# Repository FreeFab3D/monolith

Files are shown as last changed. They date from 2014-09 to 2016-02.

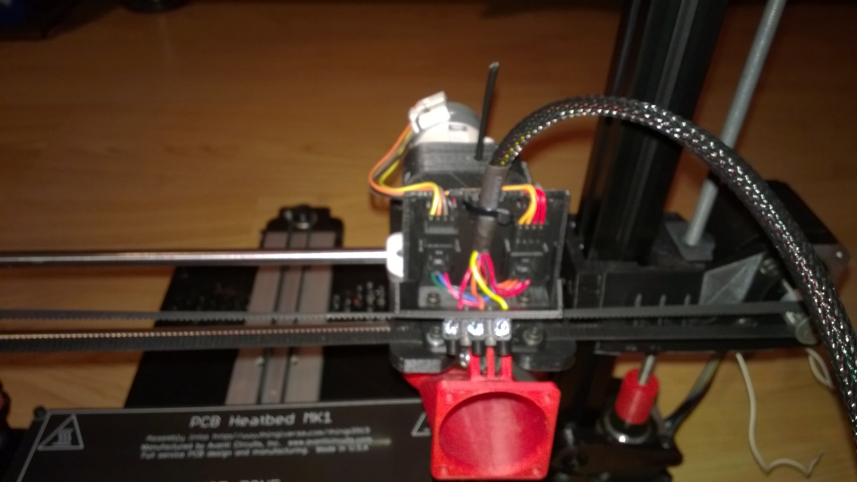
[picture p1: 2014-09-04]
build photos/WP_20140312_003.jpg

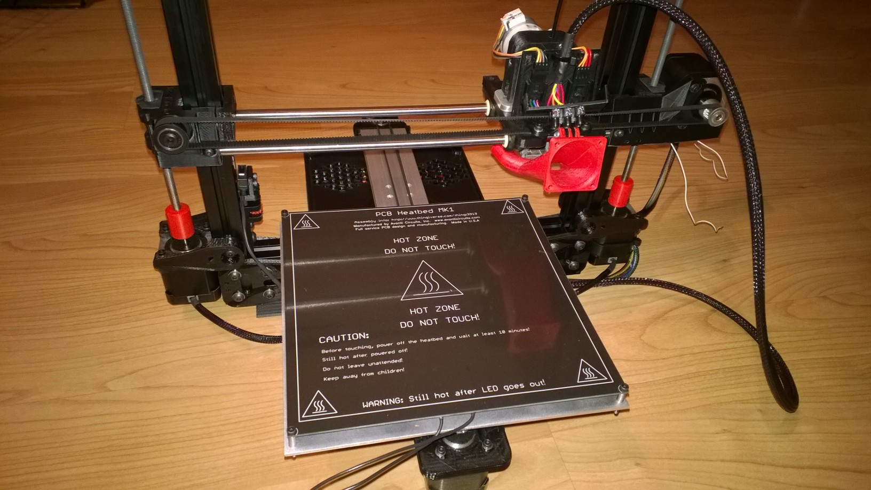
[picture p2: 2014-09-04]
build photos/WP_20140312_004.jpg

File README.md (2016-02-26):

# FreeFab 3D Monolith 3D Printer

## Features
- Hybrid design combining the best of the Bukobot and MendelMax
- 200mm x 200mm x 200mm (8" x 8" x 8") build area
- 120mm/minute speed
- 0.1 - 0.25mm layer height
- 3mm filament-based feed stock
- Heated bed to print ABS, PLA and other plastics
- Hexagon hot-end and RAMBo control board
- Flexible and advanced open-source design, including a USB interface
- LED extrusion lamps
- Compact precision aluminum frame

## Repo Layout

### Build Photos
Various photos showing close-ups of the machine to help while building. 

### Firmware
Marlin firmware for the RAMBo Arduino control boards. One version is for the Monoliths using an LCD displau board.

### Settings
Screen shots showing settings for Repetier-Host and Slic3r config ini profiles. 

### STLs
All the plastic parts required to build the Monolith. In some cases more than one version of the same part are included, ie: Y-foot and Z-rod caps. You can choose which version you like best. 

All parts should be printed using good quality ABS except the control board box and lid, which should be printed in PLA. Micro extruder needs at least 30% infill (40% is better), but other parts should use between 20% and 30% infill. 

This work is licensed under a Creative Commons Attribution 4.0 International License.

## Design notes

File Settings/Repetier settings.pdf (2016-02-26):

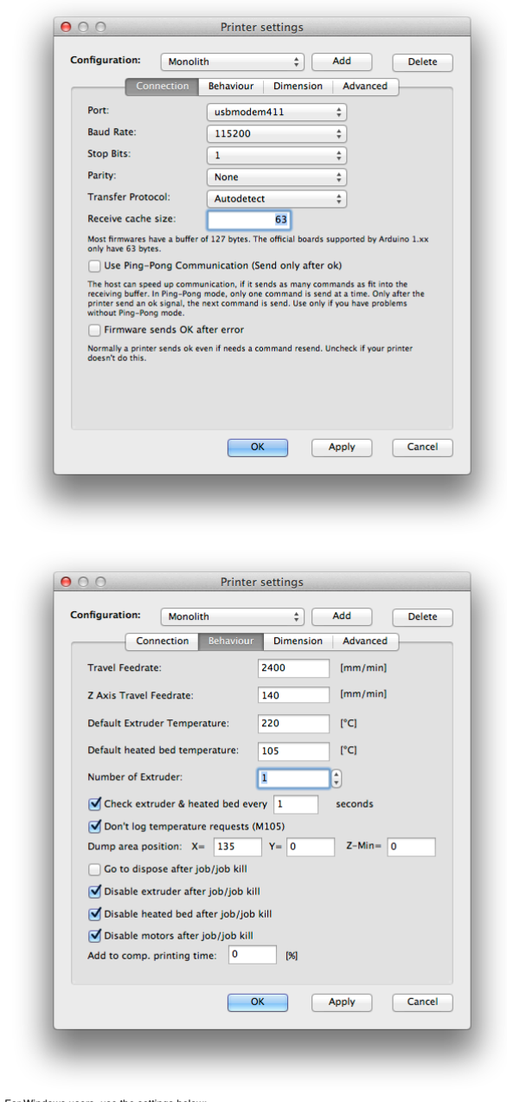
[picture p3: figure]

For Windows users, use the settings below:

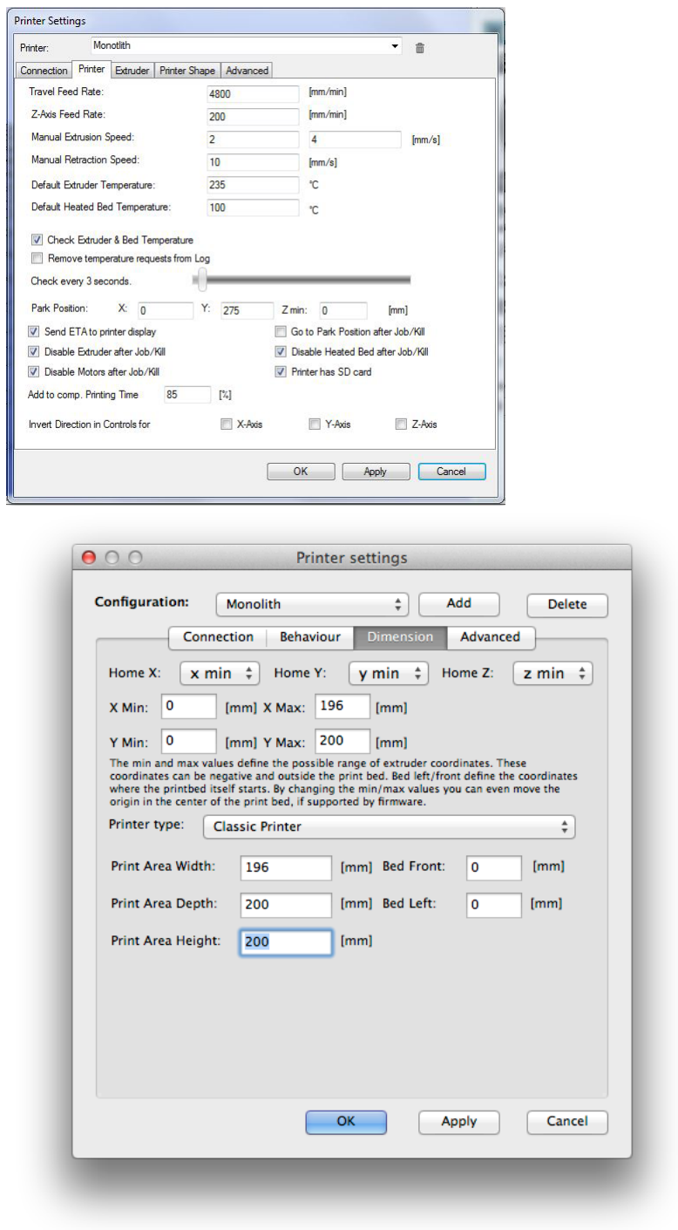
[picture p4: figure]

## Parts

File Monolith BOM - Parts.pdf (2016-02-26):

ML1 Parts | Qty. | Description | Mfg. Part # | Unit cost | Ext. Cost | Supplier | Comments
Frame | 2 | Aluminum Frame - side rails | HFSB5-2525-460 | $7.68 | $15.36 | us.misumi-ec.com | no price break <20+
| 1 | Aluminum Frame - top rail | HFSB5-2525-285 | $4.72 | $4.72 | us.misumi-ec.com | Price break @10
| 1 | Aluminum Frame - bottom rail | HFSB5-2550-285 | $8.04 | $8.04 | us.misumi-ec.com | Price break @10
| 1 | Aluminum Frame - y axis | HFSQN4-1050-345 | $5.96 | $5.96 | us.misumi-ec.com | no price break <75
| 2 | Smooth Rods | PSFG8-375 | $7.17 | $14.34 | us.misumi-ec.com | Price break @4 - Old rods were RGOC8-375
Printbed | 1 | Y carriage Plate | 8.625 with hole pattern | $11.15 | $11.15 | Laserfab.net | Price includes shipping.
| 1 | Y Glass | 8.375 x 7.9375 x .125" | $4.00 | $4.00 | St Pete Glass & Mirror, 5565 64th Way N, St Pete
| 1 | PCB Black | custom order | $26.00 | $26.00 | AvantiCircuits.com | Price includes shipping.
Pulleys | 2 | Pulley - 20 tooth aluminum | 210 | $5.50 | $11.00 | OpenBuilds.com | Possible alt = B&B Manufacturing
Belts | 4' | 6mm GT2 Belt | GT2 Timing Belt | $2.66 | $10.64 | Ultibots.com | Price break @20m
X Idler | 1 | Vslot Idler | 550-PACK | $4.85 | $4.85 | OpenBuilds.com | Price break @20
Wheels | 4 | Vslot Wheel Kits - Delrin | 500-Pack | $4.13 | $16.50 | OpenBuilds.com | Price break @20 - Includes Shipping
| 4 | Spacer, #10 hole, 1/4" tall, AL | 6TA23 | $0.42 | $1.69 | Grainger | Price includes shipping
Bearings | 5 | 8mm x 22mm 608-ZZ Bearing | 0474510 | $0.79 | $3.94 | Fastenal
| 4 | Pillow block bearing | KSTM-08 | $2.54 | $10.16 | Igus.com
Extruder motor | 1 | PG35L geared stepper motor | PG35L | $23.70 | $23.70 | Ultibots.com | Price break @5
Heat sink | 1 | PG35L short fin heat sink | PG35L short fin heat sink | $7.95 | $7.95 | Ultibots.com
Extruder hardware | 1 | Micro-extruder kit | MEV5HWK3 | $22.95 | $22.95 | Ultibots.com | Price break @4
Fans, extruder & box | 2 | Fan - 40x40x10mm 12v 8cfm | | $2.32 | $4.64 | Amazon | $2.84 FolgerTech; $2.95 Ultibots
| 1 | Fan - 25x25x10mm 12v | | $2.59 | $2.59 | Amazon | $5.00 SeeMeCNC - Comes with Hexagon?
Rambo | 1 | Rambo V1.1b | $85.00 | $85.00 | RepRapElectro.com | Price break @10
Nema 17 | 0 | Nema-17 Stepper Motors | 817752011303 | $13.95 | $0.00 | Lulzbot.com
| 4 | Nema-17 Stepper Motors | MNEMA17-40 | $6.80 | $27.20 | RobotDigg | $10.30 inc shipping
Hotend | 0 | Budaschnozzle 2.0 w/ .35 nozzle | 817752014212 | $95.00 | $0.00 | Lulzbot.com
| 1 | Hexagon w/ .4 nozzle | Hexagon | $35.00 | $35.00 | RepRapDiscount.com | Price break @10
Power Supply | 1 | 12vDC 16A PSU w/ 4pin plug | 817752012478 | $45.00 | $45.00 | Lulzbot.com
| 1 | DIN 4-pin female receptacle | 817752012485 | $2.50 | $2.50 | Lulzbot.com
Wiring | 12" | #14 str ins CU (red & black) - 12" | | | $0.00 | Carman | local purchase as needed - no bulk supplier yet
| 4 | #14 female blade crimp connector | A27828-ND | $0.24 | $0.95 | Fastenal | 0.16 > 100; 58568 = Fastenal
| 84" | #24 CU stranded coated (red) | | | $0.00 | Carman | Red
| 42" | #24 CU stranded coated (others) | | | $0.00 | Carman | Orange, Yellow, Green, Blue, Black
| 1 | Rocker Switch | CH784-ND | $1.37 | $1.37 | Digikey.com | 1.43 > 10; 1.37 >25
| 2 | Molex female 4-pin housing | WM6676-ND | $0.73 | $1.46 | Digikey.com | 1.06 > 10 - use with pin WM2517
| 8 | Molex male pin | WM2517CT-ND | $0.08 | $0.68 | Digikey.com | 0.08 > 100 - use with housing WM6676
| 0 | Molex male 4-pin housing | WM5329-ND | $0.34 | $0.00 | Digikey.com | 0.335 > 25 (usually comes w/board) - use with pin WM2573
| 0 | Molex female pin | WM2573CT-ND | $0.16 | $0.00 | Digikey.com | 0.157 > 100 (some come w/board) - with housing WM5329
| 1 | Molex male 2-pin header | WM4000-ND | $0.16 | $0.16 | Digikey.com | 0.164 > 50
| 0 | Molex 2-pin housing | WM2800-ND | $0.32 | $0.00 | Digikey.com | 0.2696 > 25 (usually comes with endstops) - use with pin WM2573
| 3 | Eurostyle Terminal Strip | 0765017 | $0.09 | $0.28 | Fastenal | 3240169-ND Digikey
| 18" | 1/2" PET Braided Sleeving | X000FEJPET | $0.26 | $4.68 | Amazon/ElectriDuct Inc. | 100' roll, $25.99
| 24" | 1/4" PET Braided sleeving | BS-XO-025-BK-100 | $0.23 | $5.52 | ElectriDuct Inc. | 100' roll, $22.99
| 2" | 1/2" heat shrink tubing | 0705396 | $0.10 | $0.19 | Fastenal | 20 x 6" / $11.53 = $0.096 per inch
| 6" | 1/4" heat shrink tubing | 0705394 | $0.07 | $0.43 | Fastenal | 26 x 6" / $11.16 = $0.072 per inch
Lighting | 1' | Blue LEDs | AR-ST224BLU | $0.00 | $0.00 | Frontier Lighting | Aurora Lighting Product - $6.40/ft
| 0.5' | White LEDs | ??? | $0.00 | $0.00 | Frontier Lighting | Aurora Lighting Product

Springs

4

Compression Spring 302-SS OD-0.18" WD-0.022" FL- 0.69" CL-
0.365" L-2.61# R-8# | B005KSQ4H0 | $1.20 | $4.79
Compression Spring | 302 Stainless | OD 0.18" | Wire Size 0.022" |
Free Length 0.69" | Compressed 0.365" | Load 2.61# | Rate 8#
Filament | 1 | One free roll of PLA filament | $31.00 | $31.00

ML1 Parts | Qty. | Description | Mfg. Part # | Unit cost | Ext. Cost | Supplier | Comments
Total | | | | | $504.91
| | | | | $27.85 | Total from Screws Page
| | | | | $20.69 | Total from Toolkit Page

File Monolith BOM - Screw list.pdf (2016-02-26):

ML1 Screws | Total / Machine | X Axis | Y Axis | Z Axis | Extruder & X Carriage | Other | Comments | Supplier | Part # | Price | Cost / machine
M3-06 BH | 12 | 4 | | | | 8 | Electronic box and board | Fastenal | 40867 | 0.1549 | 1.8588
M3-08 SH | 6 | | | | | | | Fastenal | 1139503 | 0.1211 | 0.7266
M3-10 SH | 20 | 4 | 4 | 8 | 4 | | | Fastenal | 1139504 | 0.1211 | 2.422
M3-12 SH | 27 | 8 | | | 12 | 7 | Box fan (4) Wire retainer (3) | Fastenal | 1139505 | 0.1258 | 3.3966
M3-15 SH | 4 | | | | 4 | | | Fastenal | 0163619 | 0.1581 | 0.6324
M3-20 SH | 4 | | 4 | | | | | Fastenal | 1139507 | 0.1388 | 0.5552
M3-25 SH | 4 | | 4 | | | | | Fastenal | 1139508 | 0.1607 | 0.6428
M3 Flat Washers | 16 | | 4 | 8 | 4 | | | Fastenal | 40217 | 0.0112 | 0.1792
M3 Hex Nuts | 12 | | | | 12 | | | Fastenal | 1140302 | 0.0263 | 0.3156
M3 Heat Inserts | 23 | 12 | 3 | | | 8 | | Fastenal | 11125995 | 0.0898 | 2.0654
#4 Split Washers (3mm) | 4 | | 4 | | | | PCB to bed attachment | Fastenal | 1133606 | 0.0172 | 0.0688

M4-18 SH | 2 | | | | 2 | | | Fastenal | 1139519 | 0.1271 | 0.2542
M4-20 BH | 0 | | | | | | | Fastenal | 1139903 | 0.0965 | 0
M4 Flat Washers | | | | | | | | Fastenal | 1140353 | 0.0176 | 0
M4 Slim Nuts | | | | | | | | Fastenal | 0141486 | 0.0153 | 0
M5-08 BH | 5 | | 5 | | | | Mounts Y-rail to frame | Fastenal | 40876 | 0.1169 | 0.5845
M5-10 BH | 40 | | 4 | 4 | | 32 | Frame | Fastenal | 1139905 | 0.1669 | 6.676
M5-10 SH | 2 | | | | | 2 | Filament Reel | Fastenal | 1139544 | 0.1092 | 0.2184
M5-12 BH | 4 | | | | | 4 | | Fastenal | 1140877 | 0.1699 | 0.6796
M5-16 BH | 4 | | | | | 4 | Box lid to 10x50 | Fastenal | 1140879 | 0.1552 | 0.6208
M5-25 BH | 4 | | | | | 4 | Attach Delrin wheels to AL plate | Fastenal | 40881 | 0.1596 | 0.6384
M5 Slim Nuts | 40 | | 4 | 4 | | 32 | Frame | Fastenal | 0141487 | 0.0323 | 1.292
M5 T-Nuts | 2 | | 2 | | | | Mounts Y-rail to frame | Misumi | HNKK5-5 | 0.1526 | 0.3052
M5 Flat Washers | 4 | | | | | 4 | | Fastenal | 40219 | 0.0152 | 0.0608
M6 Nut | 0 | | | | | | | McMaster-Carr | 90591A151 | 0.023 | 0
M6 Threaded Rod | 0.667 | | | 0.667 | | | | Fastenal | MR2551000A4000 | 5.485 | 3.658495

27.85179
Total per Machine 5

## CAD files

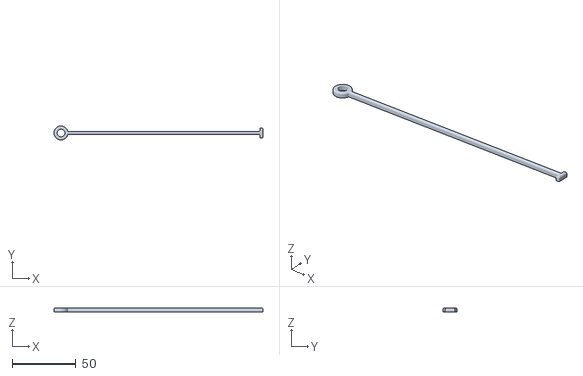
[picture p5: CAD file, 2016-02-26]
STLs/Frame and Electronics/main harness support band.stl
163.3 x 11.0 x 3.00

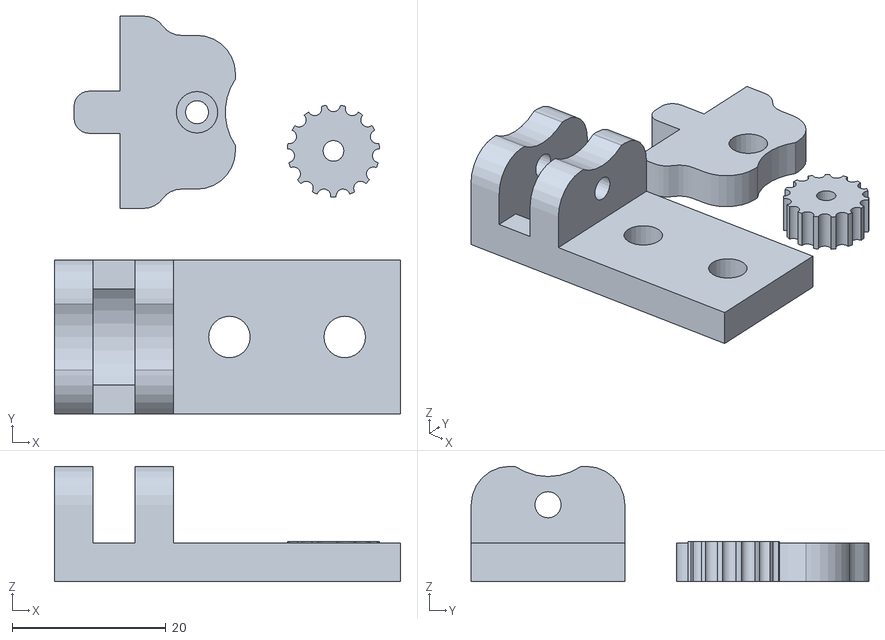
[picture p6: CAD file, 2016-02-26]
STLs/Z axis/Stop assembly.stl
45.0 x 51.7 x 15.0

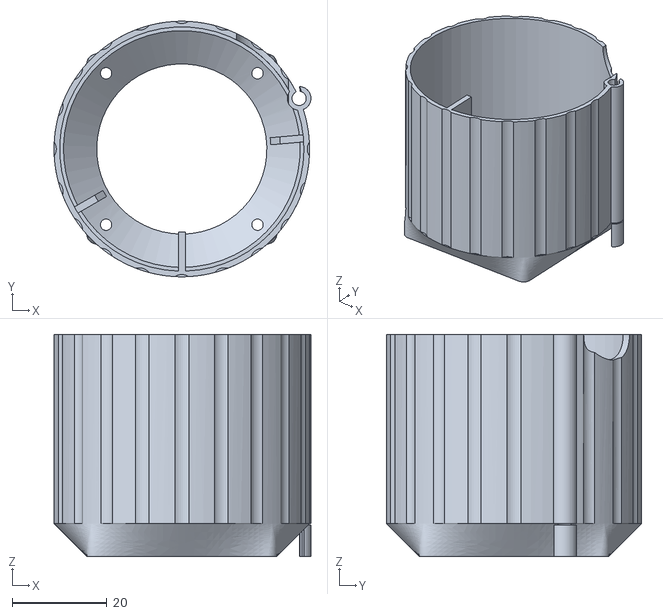
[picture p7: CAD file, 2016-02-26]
STLs/Small Parts/New PG35 Fan Shroud.STL
54.3 x 54.0 x 47.0

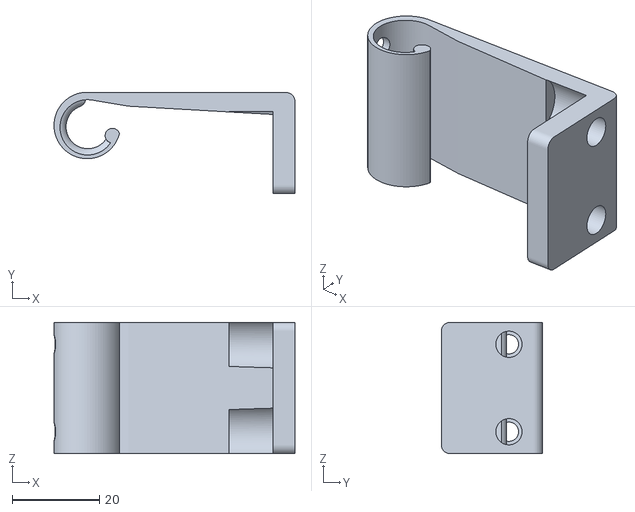
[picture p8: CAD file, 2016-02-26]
STLs/Y axis/Foot Y updated 10515.stl
55.1 x 23.2 x 30.0

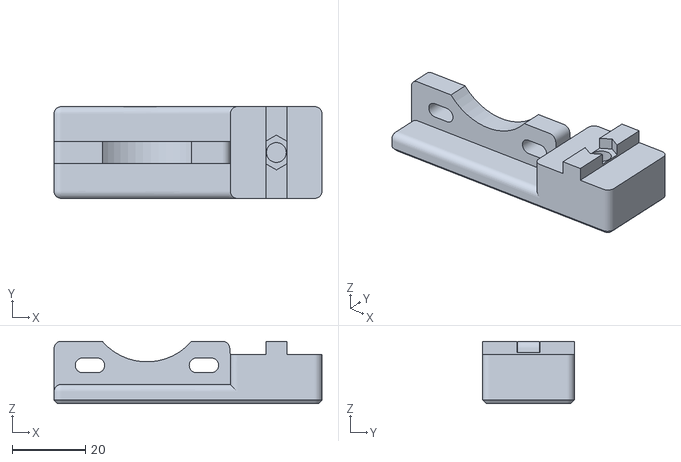
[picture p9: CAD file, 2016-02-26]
STLs/Z axis/z_motor_mount.stl
73.0 x 25.0 x 17.0

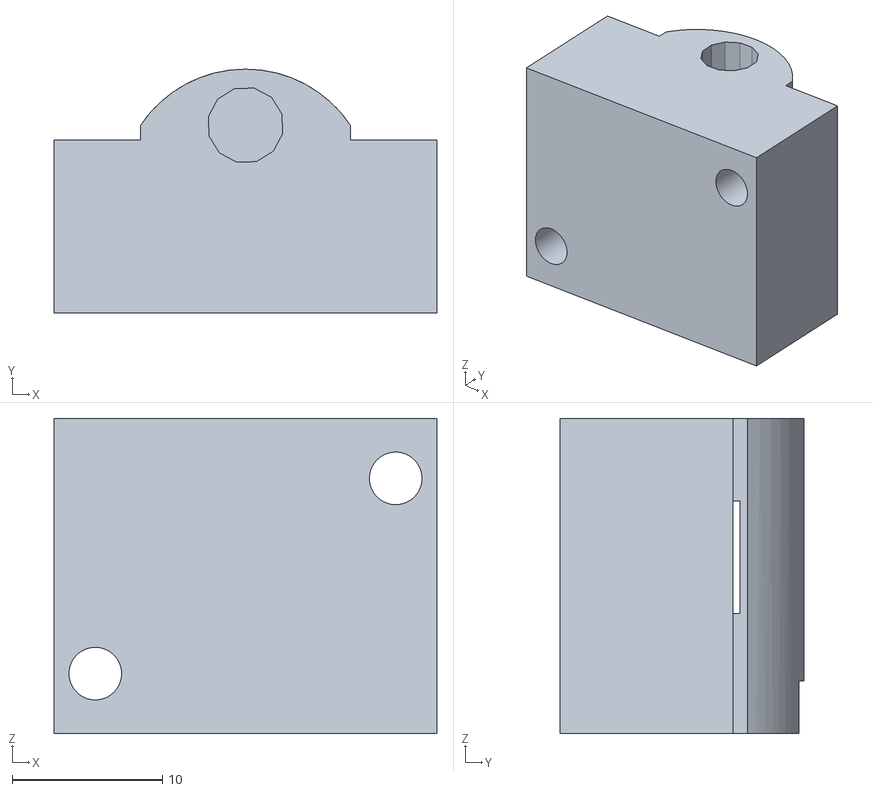
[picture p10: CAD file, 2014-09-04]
STLs/Micro extruder/me_idler_v2_624.stl
25.5 x 16.2 x 21.0

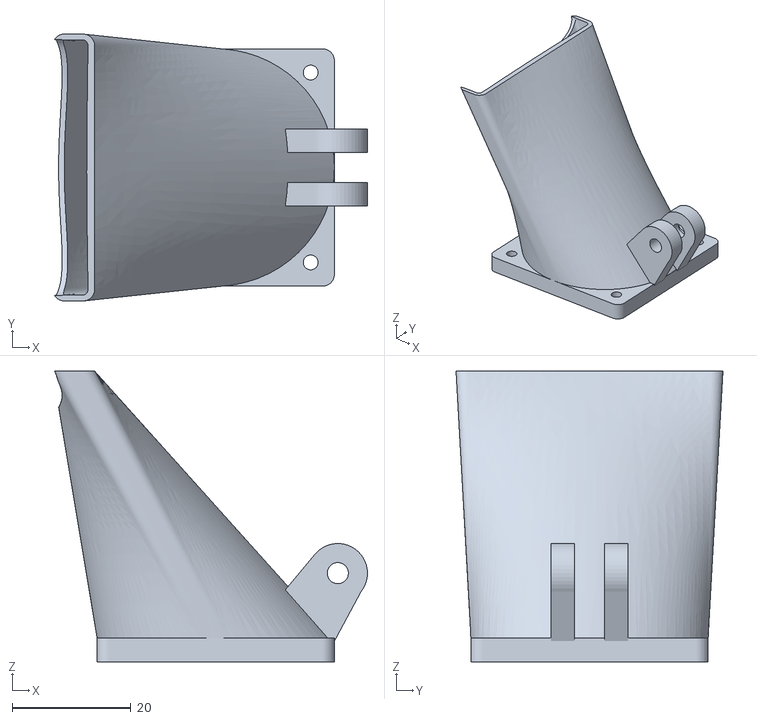
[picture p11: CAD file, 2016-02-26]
STLs/Small Parts/Single Arm Fan Duct Longer.STL
52.8 x 45.0 x 49.0

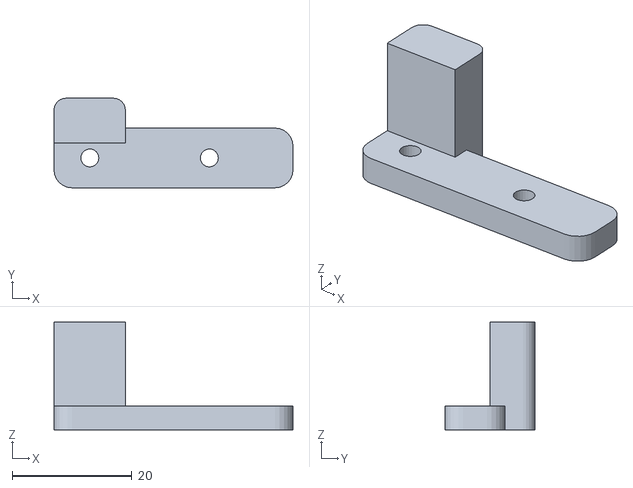
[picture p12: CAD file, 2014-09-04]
STLs/Y axis/Y stop trigger.stl
40.0 x 15.0 x 18.0

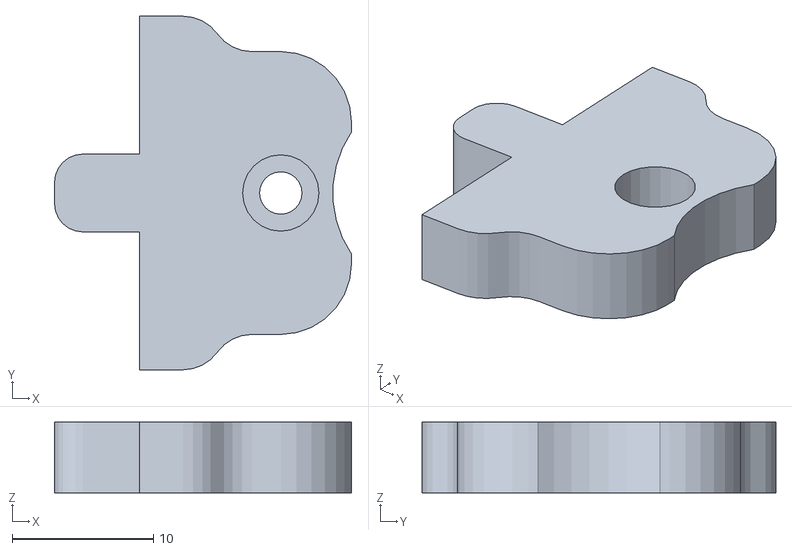
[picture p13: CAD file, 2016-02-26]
STLs/Z axis/Z stop top plate ML1 wider .stl
21.0 x 25.0 x 5.00

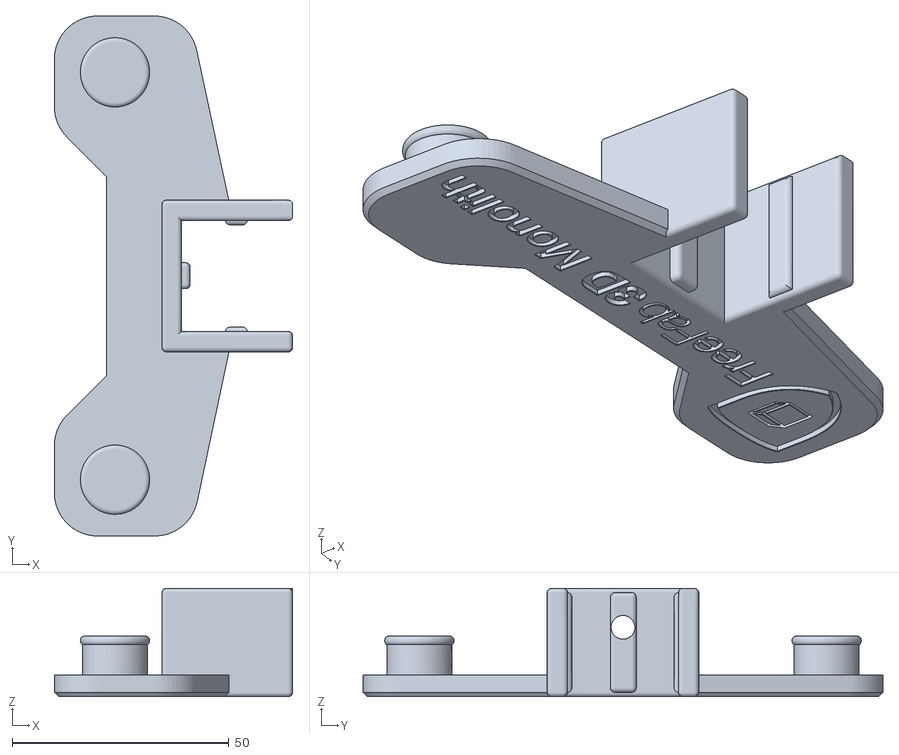
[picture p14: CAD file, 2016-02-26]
STLs/Frame and Electronics/compact filament holder.stl
55.0 x 120.0 x 25.0

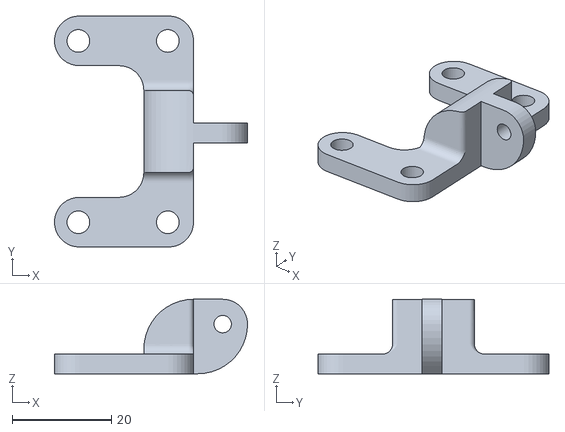
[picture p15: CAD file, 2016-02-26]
STLs/Small Parts/Fan Mount.STL
38.9 x 46.5 x 15.0

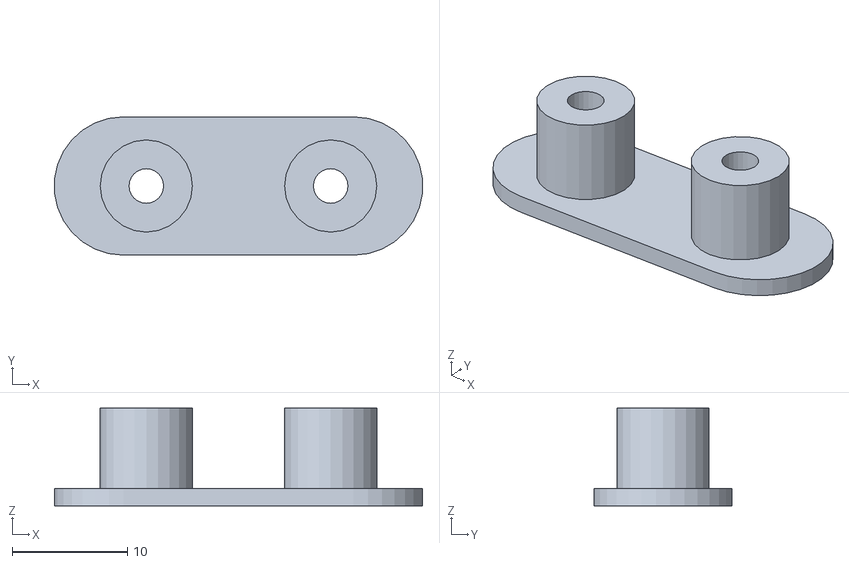
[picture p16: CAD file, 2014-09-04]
STLs/Y axis/Y belt attachment.stl
31.9 x 12.0 x 8.50

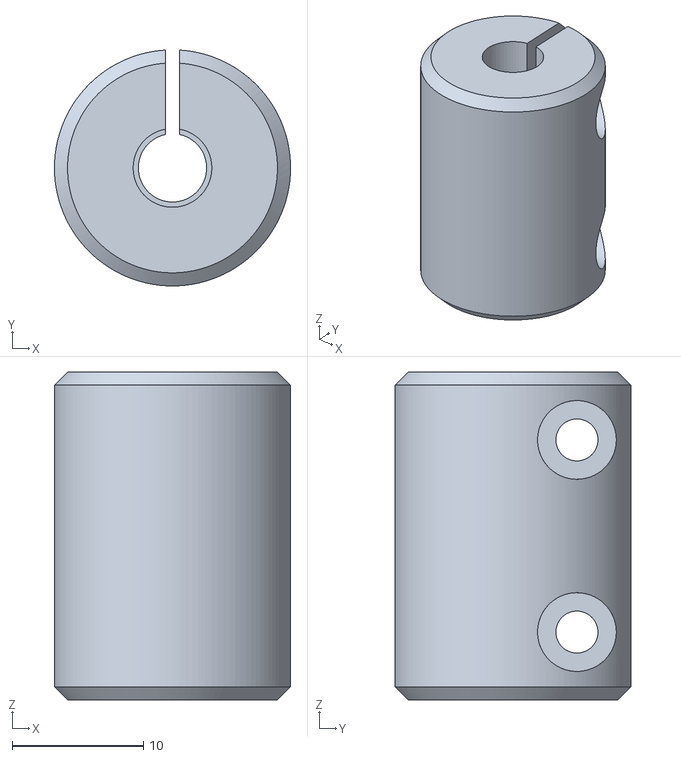
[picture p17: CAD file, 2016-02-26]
STLs/Z axis/Coupler.stl
18.0 x 18.0 x 25.0

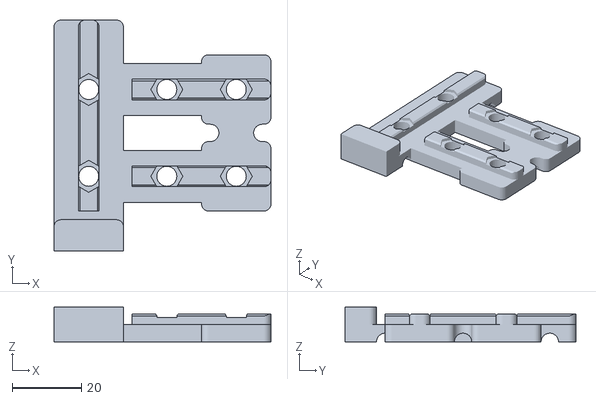
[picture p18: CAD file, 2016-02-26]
STLs/Frame and Electronics/bottom right bracket.stl
62.5 x 66.5 x 10.00

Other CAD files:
STLs/Small Parts/Cap with 3 pins top of 8020.stl
STLs/X axis/X motor mount bracket (1).stl
STLs/Y axis/Y stop holder.stl
STLs/Z axis/Z stop buttom shorter.stl
STLs/Frame and Electronics/Angle bracket Y to frame.stl
STLs/Frame and Electronics/Box Top.stl
STLs/Frame and Electronics/Full Box new rambo screw pos1mm.STL
STLs/Frame and Electronics/Misumi plugs.stl
STLs/Frame and Electronics/Monolith_strain_relief-v1.1.stl
STLs/Frame and Electronics/Thread rod top cover.stl
STLs/Frame and Electronics/bottom left bracket.stl
STLs/Frame and Electronics/top_left_bracket.stl
STLs/Frame and Electronics/top_right_bracket.stl
STLs/Micro extruder/New ME bearing position ML1 bigger nut cavity.stl
STLs/Small Parts/Bed cable clamp.stl
STLs/Small Parts/Cable guide sping to frame.stl
STLs/Small Parts/Cable slider.stl
STLs/Small Parts/Misumi plugs.stl
STLs/Small Parts/Springamathing1_Med_5in.stl
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

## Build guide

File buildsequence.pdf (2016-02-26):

Gather parts and cut belts, wires and LED strips.

Set all heat inserts into proper locations

While assembling, drill and/or tap various holes and sand/file parts as needed.

Attach frame brackets and insert T nuts into frame along with Z stop adjuster

Attach Y rail and y axis stabilizer

Assemble x carriage and x ends and install into frame

Attach box lid to Y rail

Assemble bed plate and attach to Y rail

Attach Y ends and Y end stops

Attach Z motor mounts and add Z motors and add top LED strip wires and strip

Attach z threaded rods

Put control board into box and add power wires, receptical and power switch (this can be moved up on the list as we can have them pre assembled)

Attach box to frame with rino clips

Start running wires from motors, endstops, lighting and fans while adding wire connectors.

Attach belts to X and Y axis

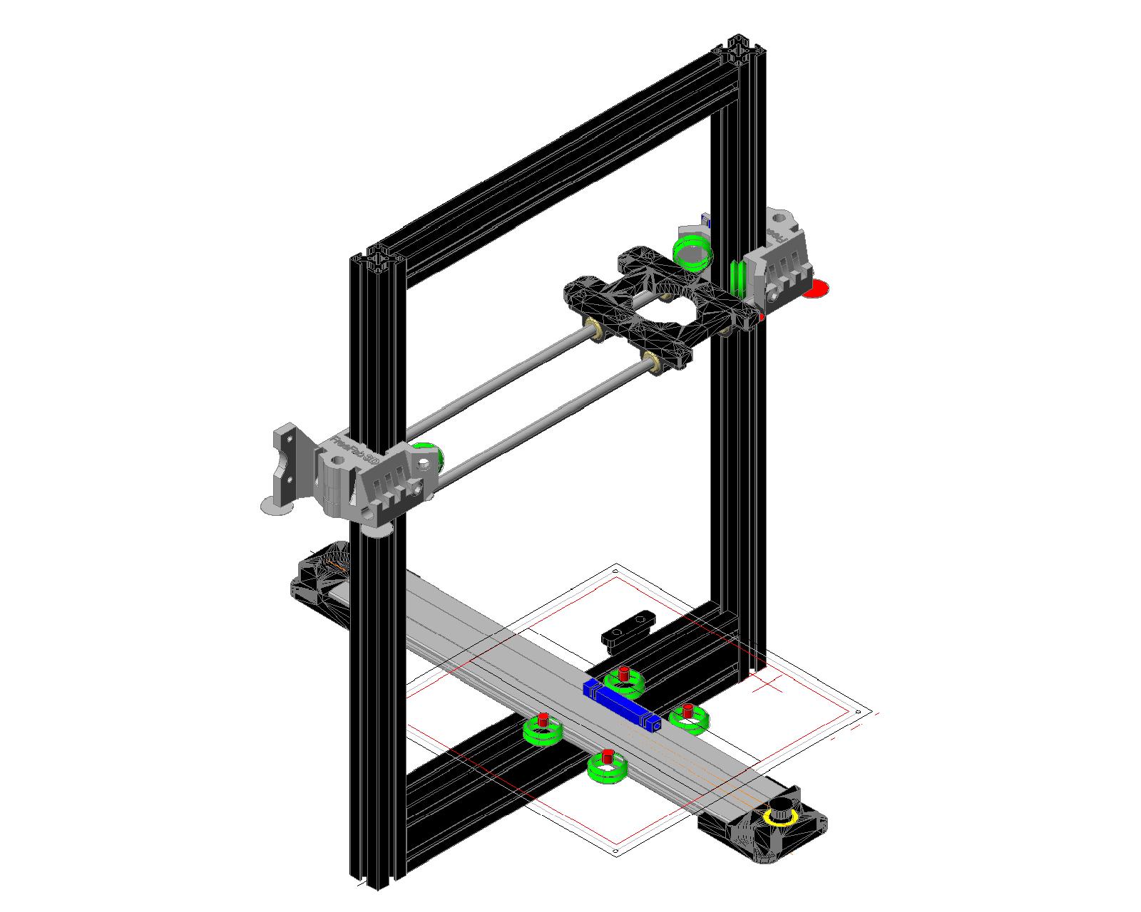
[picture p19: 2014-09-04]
build photos/Frame-Model2 copy.jpeg

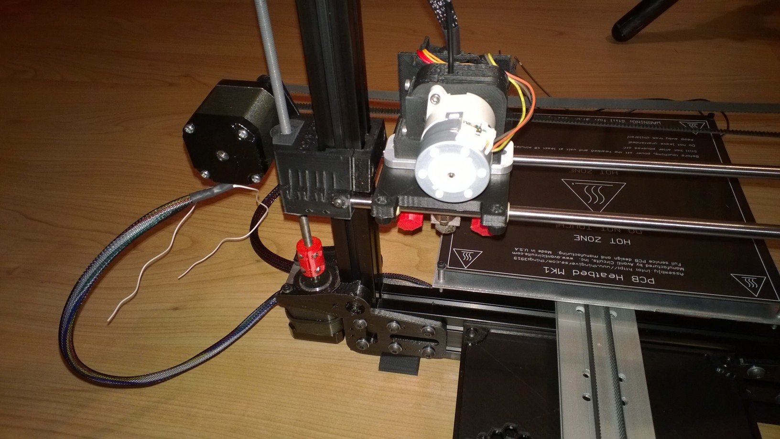
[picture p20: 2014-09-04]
build photos/WP_20140312_002.jpg

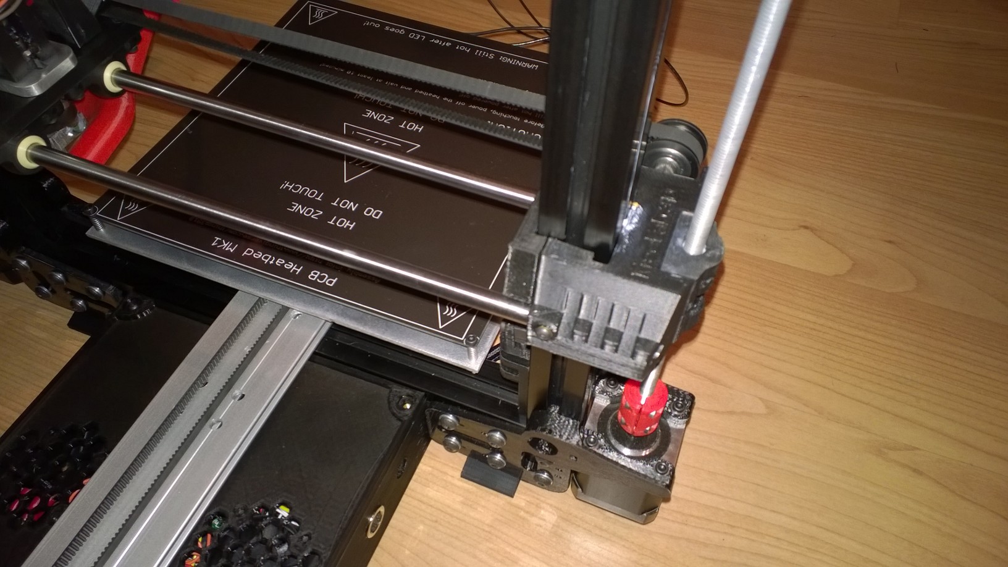
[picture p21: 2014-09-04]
build photos/WP_20140312_001.jpg

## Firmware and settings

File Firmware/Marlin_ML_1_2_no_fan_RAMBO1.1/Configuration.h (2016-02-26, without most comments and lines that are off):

#define CONFIGURATION_H
#define STRING_VERSION_CONFIG_H __DATE__ " " __TIME__ // build date and time
#define STRING_CONFIG_H_AUTHOR "(Fri ML1-2 Rambo LCD" // Who made the changes.
#define SERIAL_PORT 0
#define BAUDRATE 115200
#define MOTHERBOARD 301
 #define CUSTOM_MENDEL_NAME "MonoLith FF3D"
#define EXTRUDERS 1
#define POWER_SUPPLY 1
#define TEMP_SENSOR_0 7 //used to be 1 for the E3D
#define TEMP_SENSOR_1 7
#define TEMP_SENSOR_2 7
#define TEMP_SENSOR_BED 1
#define MAX_REDUNDANT_TEMP_SENSOR_DIFF 10
#define TEMP_RESIDENCY_TIME 10  // (seconds)
#define TEMP_HYSTERESIS 3       // (degC) range of +/- temperatures considered "close" to the target one
#define TEMP_WINDOW     1       // (degC) Window around target to start the residency timer x degC early.
#define HEATER_0_MINTEMP 5
#define HEATER_1_MINTEMP 5
#define HEATER_2_MINTEMP 5
#define BED_MINTEMP 5
#define HEATER_0_MAXTEMP 275
#define HEATER_1_MAXTEMP 275
#define HEATER_2_MAXTEMP 275
#define BED_MAXTEMP 110
#define PIDTEMP
#define BANG_MAX 255 // limits current to nozzle while in bang-bang mode; 255=full current
#define PID_MAX 255 // limits current to nozzle while PID is active (see PID_FUNCTIONAL_RANGE below); 255=full current
  #define PID_FUNCTIONAL_RANGE 10 // If the temperature difference between the target temperature and the actual temperature
  #define PID_INTEGRAL_DRIVE_MAX 255  //limit for the integral term
  #define K1 0.95 //smoothing factor within the PID
  #define PID_dT ((16.0 * 8.0)/(F_CPU / 64.0 / 256.0)) //sampling period of the temperature routine
    #define  DEFAULT_Kp 77.23 //Jhead 230 with Abs in the nozzle
    #define  DEFAULT_Ki 4.30
    #define  DEFAULT_Kd 346.71
#define PIDTEMPBED
#define MAX_BED_POWER 255 // limits duty cycle to bed; 255=full current
    #define  DEFAULT_bedKp 578.60
    #define  DEFAULT_bedKi 113.18
    #define  DEFAULT_bedKd 739.45
#define PREVENT_DANGEROUS_EXTRUDE
#define PREVENT_LENGTHY_EXTRUDE
#define EXTRUDE_MINTEMP 170
#define EXTRUDE_MAXLENGTH (X_MAX_LENGTH+Y_MAX_LENGTH) //prevent extrusion of very large distances.
#define ENDSTOPPULLUPS // Comment this out (using // at the start of the line) to disable the endstop pullup resistors
  #define ENDSTOPPULLUP_XMAX
  #define ENDSTOPPULLUP_YMAX
  #define ENDSTOPPULLUP_ZMAX
  #define ENDSTOPPULLUP_XMIN
  #define ENDSTOPPULLUP_YMIN
  #define ENDSTOPPULLUP_ZMIN
const bool X_MIN_ENDSTOP_INVERTING = false; // set to true to invert the logic of the endstop.
const bool Y_MIN_ENDSTOP_INVERTING = false; // set to true to invert the logic of the endstop.
const bool Z_MIN_ENDSTOP_INVERTING = false; // set to true to invert the logic of the endstop.
const bool X_MAX_ENDSTOP_INVERTING = false; // set to true to invert the logic of the endstop.
const bool Y_MAX_ENDSTOP_INVERTING = false; // set to true to invert the logic of the endstop.
const bool Z_MAX_ENDSTOP_INVERTING = false; // set to true to invert the logic of the endstop.
#define DISABLE_MAX_ENDSTOPS
#if defined(COREXY) && !defined(DISABLE_MAX_ENDSTOPS)
  #define DISABLE_MAX_ENDSTOPS
#endif
#define X_ENABLE_ON 0
#define Y_ENABLE_ON 0
#define Z_ENABLE_ON 0
#define E_ENABLE_ON 0 // For all extruders
#define DISABLE_X false
#define DISABLE_Y false
#define DISABLE_Z false
#define DISABLE_E false // For all extruders
#define INVERT_X_DIR false    // for Mendel set to false, for Orca set to true
#define INVERT_Y_DIR false   // for Mendel set to true, for Orca set to false
#define INVERT_Z_DIR false     // for Mendel set to false, for Orca set to true
#define INVERT_E0_DIR false   // for direct drive extruder v9 set to true, for geared extruder set to false
#define INVERT_E1_DIR false    // for direct drive extruder v9 set to true, for geared extruder set to false
#define INVERT_E2_DIR false   // for direct drive extruder v9 set to true, for geared extruder set to false
#define X_HOME_DIR -1
#define Y_HOME_DIR -1
#define Z_HOME_DIR -1
#define min_software_endstops true // If true, axis won't move to coordinates less than HOME_POS.
#define max_software_endstops true  // If true, axis won't move to coordinates greater than the defined lengths below.
#define X_MAX_POS 200
#define X_MIN_POS 0
#define Y_MAX_POS 200
#define Y_MIN_POS 0
#define Z_MAX_POS 200
#define Z_MIN_POS 0
#define X_MAX_LENGTH (X_MAX_POS - X_MIN_POS)
#define Y_MAX_LENGTH (Y_MAX_POS - Y_MIN_POS)
#define Z_MAX_LENGTH (Z_MAX_POS - Z_MIN_POS)
#define MANUAL_X_HOME_POS 0
#define MANUAL_Y_HOME_POS 0
#define MANUAL_Z_HOME_POS 0
#define NUM_AXIS 4 // The axis order in all axis related arrays is X, Y, Z, E
#define HOMING_FEEDRATE {50*60, 50*60, 4*60, 0}  // set the homing speeds (mm/min)
#define DEFAULT_AXIS_STEPS_PER_UNIT   {80,80,800,775}  //
#define DEFAULT_MAX_FEEDRATE          {500, 500, 5, 45}    // (mm/sec)
#define DEFAULT_MAX_ACCELERATION      {9000,9000,100,10000}    // X, Y, Z, E maximum start speed for accelerated moves. E default values are good for skeinforge 40+, for older versions raise them a lot.
#define DEFAULT_ACCELERATION          3000    // X, Y, Z and E max acceleration in mm/s^2 for printing moves
#define DEFAULT_RETRACT_ACCELERATION  3000   // X, Y, Z and E max acceleration in mm/s^2 for retracts
#define DEFAULT_XYJERK                15    // (mm/sec)
#define DEFAULT_ZJERK                 0.4     // (mm/sec)
#define DEFAULT_EJERK                 5.0    // (mm/sec)
#define EEPROM_SETTINGS
#define EEPROM_CHITCHAT
#define PLA_PREHEAT_HOTEND_TEMP 185
#define PLA_PREHEAT_HPB_TEMP 40
#define PLA_PREHEAT_FAN_SPEED 0   // Insert Value between 0 and 255
#define ABS_PREHEAT_HOTEND_TEMP 230
#define ABS_PREHEAT_HPB_TEMP 80
#define ABS_PREHEAT_FAN_SPEED 0  // Insert Value between 0 and 255
#define SOFT_PWM_SCALE 0
#include "Configuration_adv.h"
#include "thermistortables.h"

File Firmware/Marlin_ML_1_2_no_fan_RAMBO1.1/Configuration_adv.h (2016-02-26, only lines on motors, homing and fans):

#define CONTROLLERFAN_PIN 2 //Pin used for the fan to cool controller (-1 to disable)
#define EXTRUDER_0_AUTO_FAN_PIN   6  //was -1
#define ENDSTOPS_ONLY_FOR_HOMING // If defined the endstops will only be used for homing
#define X_HOME_RETRACT_MM 5
#define Y_HOME_RETRACT_MM 5
#define Z_HOME_RETRACT_MM 2
#define QUICK_HOME  //if this is defined, if both x and y are to be homed, a diagonal move will be performed initially.
#define MICROSTEP1 LOW,LOW
#define MICROSTEP2 HIGH,LOW
#define MICROSTEP4 LOW,HIGH
#define MICROSTEP8 HIGH,HIGH
#define MICROSTEP16 HIGH,HIGH
#define MICROSTEP_MODES {16,16,4,16,16} // [1,2,4,8,16]
#define DIGIPOT_MOTOR_CURRENT {135,135,200,130,0} // Values 0-255 (RAMBO 135 = ~0.75A, 185 = ~1A)

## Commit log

2014-09-04 initial import
    [Angle bracket Y to frame.stl, Back plate for wires cover screw on side deeper.stl, Back plate for wires new screw on side deeper.stl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]
2014-09-05 Added README and Settings folder
    [Configuration.h, Configuration_adv.h]
2016-02-26 Updated repo to latest STLs, settings, and firmware
    [Back plate for wires cover screw on side deeper.stl, Both Back Plates.stl, Cable slider.stl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]
